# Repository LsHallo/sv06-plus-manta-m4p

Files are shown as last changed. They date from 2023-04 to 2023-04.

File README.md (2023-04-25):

# BigTreeTech Manta M4P + CB1 - Sovol SV06 Plus Klipper Config

This repo contains my Sovol SV06 Plus config for use with Klipper.  
I have exchanged the stock mainboard with a Manta M4P from BigTreeTech and I am using the CB1 to control Klipper via Mainsail.  
The `printer.cfg` is attached. STL for the M4P case [is here](case/Manta%20M4P%20Sovol%20SV06%20Mount.stl).

I have modified the config found in [https://github.com/bassamanator/Sovol-SV06-firmware/tree/sv06-plus](https://github.com/bassamanator/Sovol-SV06-firmware/tree/sv06-plus)  
(You need to get the cfgs folder from his repository.)

## Contents

- [Case](#case)
- [M4P Notes](#m4p-notes)
  - [Fans](#fans)
  - [Filament Sensor](#filament-sensor)
  - [Z Stepper Motors](#z-stepper-motors)
  - [Sensorless Homing](#sensorless-homing)
  - [Z Probe Connector](#z-probe-connector)
- [CB1 Notes](#cb1-notes)
  - [Static IP](#set-static-ip-on-cb1)

## Case

I have adapted [this](https://www.printables.com/model/448123-manta-m4p-backpack) M4P case from printables to mount to the original SV06 mount points and have and egress point at the top for the flat cable that goes to the hotend. The cable is intended to be zip tied to the ledge that sticks out.    
Additionally you can find a mounting hole for an SMA antenna next to it.
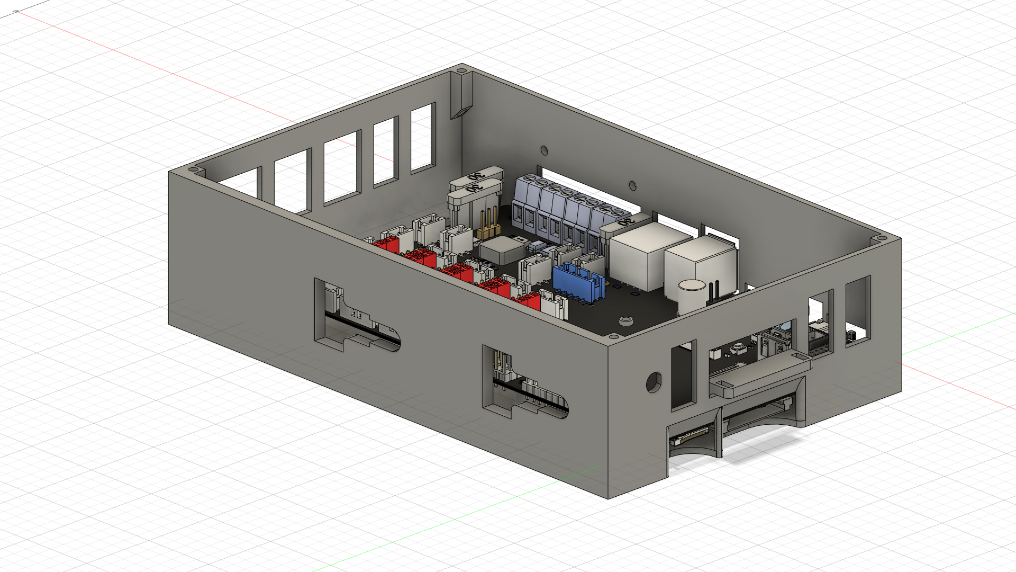
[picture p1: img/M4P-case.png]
M4P Case for Sovol SV06


## M4P Notes

### Fans

The mainboard is pin compatible with all plugs that come on the stock Sovol SV06 Plus.  
Only the hotend cooling fan (not the part cooling fan) needs to be crimped to use an JST XH 2 Pin connector. The Manta M4P came with a bag of connectors. You do not need to purchase them.  

For my config:   
The hotend cooling fan is plugged in to FAN0 on the M4P. It will turn on when you increase the temperature of the extruder. **!!Definitely verify this!!**  
The part cooling fan is plugged in to FAN2A on the M4P. It will turn on based on your GCode file.

### Filament Sensor

There are 2 filament sensor wires in the stock mainboard. One routes to the installed filament sensor near the spool.  
The other one is an optional position and routes to the right side of the hotend. You only need to plug in the one you are using into the E0-Stop connector on the M4P.

### Z Stepper Motors

Since both Z stepper motors of the SV06 Plus are crimped into the same connector you can just plug them in to the connector labelled Z on the board.

### Sensorless homing

To use sensorless homing you need to configure the TMC2209 drivers to use UART.
Set the jumpers as follows:
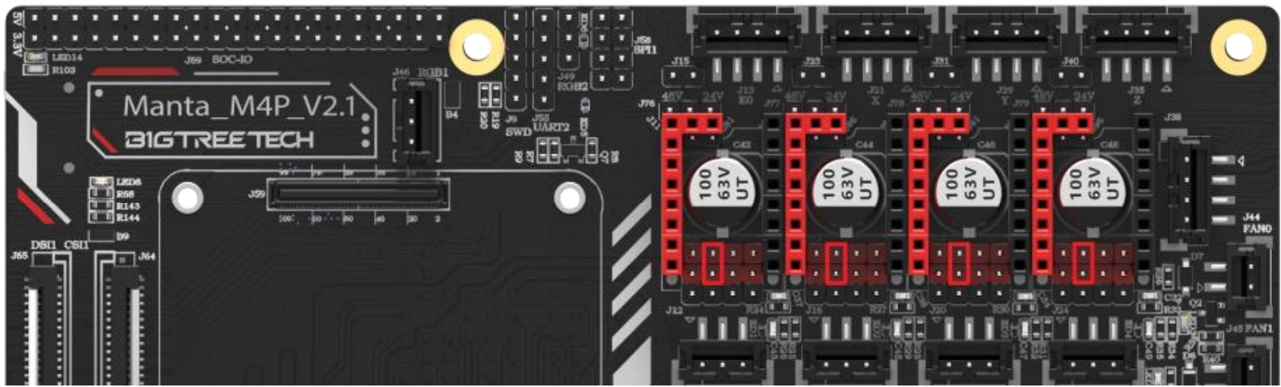
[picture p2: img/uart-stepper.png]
UART Stepper Jumper Config
  
(Mine came set from factory like this.)

Furthermore you need to set these additional jumpers:
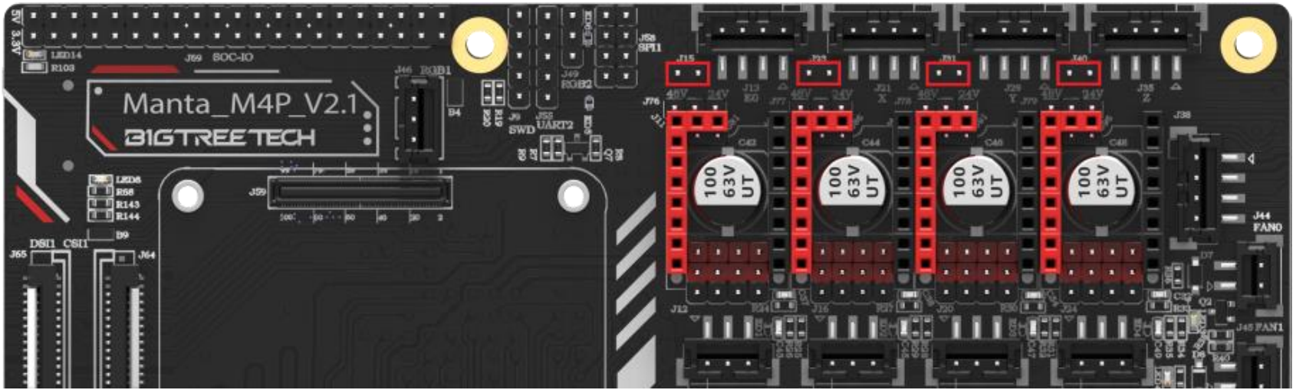
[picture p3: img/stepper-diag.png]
Stepper Diag Jumper Config
  
(I have not set the Z jumper since it uses the probe for Z homing.)

### Z Probe Connector

The Z probe connector plugs right in since it is made to be compatible with BLTouch.  
The pin used is `PC14`.

## CB1 Notes

### Set static IP on CB1

To use a static IP on the CB1 simply run `nmtui`. It is a terminal user interface for NetworkManager (comes preinstalled with the BTT CB1 images). It should look like this:  
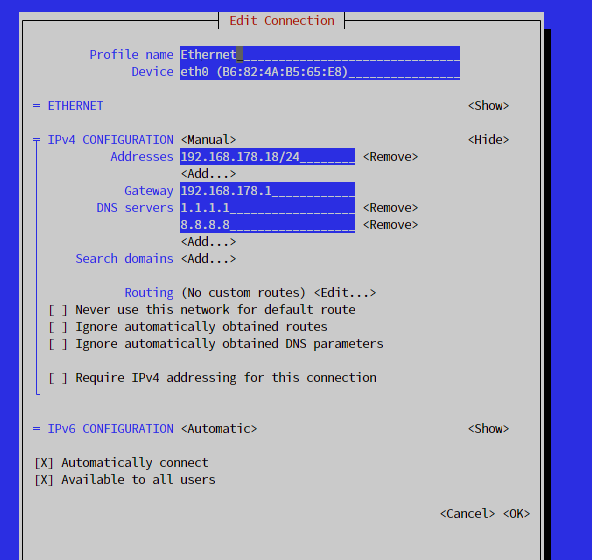
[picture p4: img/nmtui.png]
NetworkManager TUI
  
(Navigate the UI with the arrow keys and the TAB key.)

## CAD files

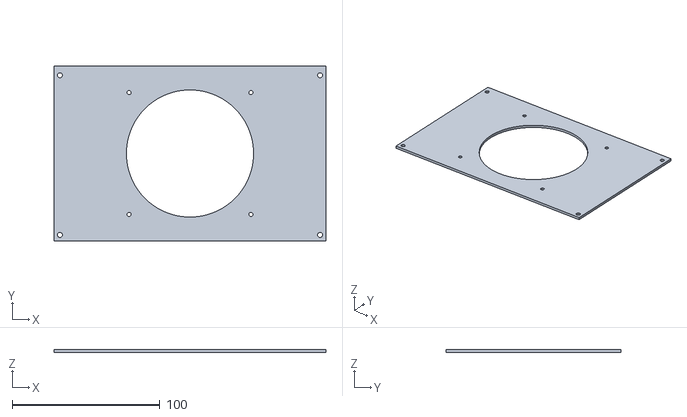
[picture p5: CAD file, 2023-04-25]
case/Manta M4P Sovol SV06 Mount Lid 92mm Fan.stl
184.0 x 118.2 x 2.00

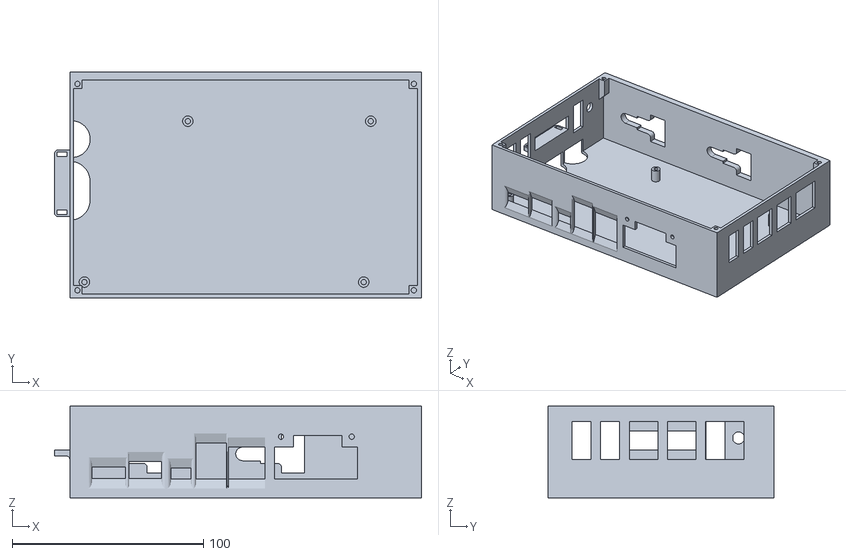
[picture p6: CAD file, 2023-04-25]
case/Manta M4P Sovol SV06 Mount.stl
192.0 x 118.2 x 48.0

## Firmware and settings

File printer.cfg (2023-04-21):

# This file contains pin mappings for the stock Sovol SV06 Plus.
# 
# Find installation instructions at https://github.com/bassamanator/Sovol-SV06-firmware
# 
# See https://www.klipper3d.org/Config_Reference.html for configuration reference.

# !!!!! IMPORTANT !!!!!
# Get these macros from https://github.com/bassamanator/Sovol-SV06-firmware/tree/sv06-plus
# !!!!! IMPORTANT !!!!!
[include ./cfgs/misc-macros.cfg]
[include ./cfgs/PARKING.cfg]
[include ./cfgs/MECHANICAL_GANTRY_CALIBRATION.cfg]

# NOTE Uncomment the ONE of the following lines if you're using an adxl345
# [include ./cfgs/adxl-rp2040.cfg]
# [include ./cfgs/adxl-direct.cfg]

[mcu]
# NOTE Obtain definition by "ls -l /dev/serial/by-id/"
# Adjust here!!!
serial: /dev/serial/by-id/usb-Klipper_stm32g0b1xx_2D001D0014504B5735313920-if00
restart_method: command

[virtual_sdcard]
path: ~/printer_data/gcodes

[printer]
kinematics: cartesian
max_velocity: 200
max_accel: 3000
max_z_velocity: 15
max_z_accel: 45
square_corner_velocity: 8.0

#####################################################################
#      X/Y/Z Stepper Settings
#####################################################################

[stepper_x]
step_pin: PC6
dir_pin: !PA14
enable_pin: !PC7
microsteps: 128
rotation_distance: 40
endstop_pin: tmc2209_stepper_x:virtual_endstop
position_endstop: 0
position_max: 300 # NOTE You can adjust this if you have more room
homing_speed: 40
homing_retract_dist: 0

[tmc2209 stepper_x]
uart_pin: PB12
run_current: 0.820
stealthchop_threshold: 0
interpolate: False
#sense_resistor: 0.150
#uart_address: 3
driver_SGTHRS: 86 # NOTE Bump sensitivity; increase to make more sensitive
diag_pin: PC0

[stepper_y]
step_pin: PB10
dir_pin: PB2
enable_pin: !PB11
microsteps: 128
rotation_distance: 40
endstop_pin: tmc2209_stepper_y:virtual_endstop
position_endstop: 0
position_max: 300 # NOTE You can adjust this if you have more room
homing_speed: 40
homing_retract_dist: 0

[tmc2209 stepper_y]
uart_pin: PC10
run_current: 0.880
stealthchop_threshold: 0
interpolate: False
#sense_resistor: 0.150
#uart_address: 3
driver_SGTHRS: 110 # NOTE Bump sensitivity; increase to make more sensitive
diag_pin: PC1

[stepper_z]
step_pin: PB0
dir_pin: !PC5
enable_pin: !PB1
microsteps: 128
rotation_distance: 4
endstop_pin: probe:z_virtual_endstop
position_min: -4
position_max: 340 # NOTE You can adjust this if you have more room
homing_speed: 5

[tmc2209 stepper_z]
uart_pin: PC9
run_current: 0.800
stealthchop_threshold: 0
interpolate: False
#sense_resistor: 0.150
#uart_address: 3
diag_pin: PC2

#####################################################################
#   Extruder
#####################################################################

[extruder]
step_pin: PB3
dir_pin: !PB4
enable_pin: !PD5
microsteps: 128
rotation_distance: 4.65 # NOTE Calibrate e-steps and adjust https://www.klipper3d.org/Rotation_Distance.html
nozzle_diameter: 0.400
filament_diameter: 1.750
heater_pin: PC8
sensor_type: EPCOS 100K B57560G104F
sensor_pin: PA0
control: pid
pid_kd: 41.96
pid_kp: 15.66
pid_ki: 1.49
min_temp: 0
max_temp: 300
max_extrude_only_distance: 150.0

[tmc2209 extruder]
uart_pin: PA13
run_current: 0.550
stealthchop_threshold: 0
interpolate: False
#sense_resistor: 0.150
#uart_address: 3

#####################################################################
#   Bed Heater
#####################################################################

[heater_bed]
heater_pin: PD8
sensor_type: EPCOS 100K B57560G104F
sensor_pin: PC4
control: pid
pid_kp: 186.38
pid_ki: 36.12
pid_kd: 637.30
min_temp: 0
max_temp: 110

#####################################################################
#   Probe Related
#####################################################################

[probe]
pin: PC14
x_offset: 27
y_offset: -20
#z_offset: 0
samples: 3
samples_result: median
samples_tolerance: 0.01
samples_tolerance_retries: 5

[safe_z_home]
home_xy_position: 123, 170
speed: 100.0
z_hop: 10
z_hop_speed: 15

[bed_mesh]
speed: 175
mesh_min: 30, 30
mesh_max: 270, 270
probe_count: 5,5
algorithm: bicubic
fade_start: 1
fade_end: 10
fade_target: 0

#####################################################################
#   Fans
#####################################################################

[fan]
pin: PD4

[heater_fan Heater_Fan]
pin: PD2

#####################################################################
#   Misc
#####################################################################

# NOTE Apparently the screen is not Klipper friendly
# [display]
# lcd_type: st7920
# cs_pin: PB12
# sclk_pin: PB13
# sid_pin: PB15
# encoder_pins: ^PB14, ^PB10
# click_pin: ^!PB2

# NOTE The speaker will not work, since the screen doesn't
# [output_pin beeper]
# pin: PC6
# value: 0
# shutdown_value: 0
# pwm: True
# cycle_time: 0.0005 ; Default beeper tone in kHz. 1 / 0.0005 = 2000Hz (2kHz)

[filament_switch_sensor filament_sensor]
switch_pin: PC15
pause_on_runout: True
insert_gcode:
    { action_respond_info("Insert Detected") }
runout_gcode:
    { action_respond_info("Runout Detected") }
    CONDITIONAL_BEEP i=3 dur=300 freq=400

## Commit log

2023-04-21 change name of heater fan
    [printer.cfg]
2023-04-21 change filament sensor pin
    [printer.cfg]
2023-04-21 remove save_config
    [printer.cfg]
2023-04-25 add case
    [Manta M4P Sovol SV06 Mount Lid 92mm Fan.stl, Manta M4P Sovol SV06 Mount.stl]
